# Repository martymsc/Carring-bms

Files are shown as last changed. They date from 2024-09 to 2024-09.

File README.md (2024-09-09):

# Carring-bms
Bms system for lithium based cells. Carring because it cares :D

The bms is based on an arduino leonardo board from Longan Labs (https://www.longan-labs.cc/1030008.html) and a battery monitor IC from Texas Instruments called BQ76PL455A.

Current revision:
 <ul>
  <li>  Battery cells voltage readout over serial</li>
  <li>  OV and UV protection with contactor control</li>
  <li>  Precharge circuit contorl</li>
  <li>  Isolation between contol MCU and battery  </li>
  <li>  Mcu supply is from the car, bms ic is powered by the battery </li>
 </ul> 
  
Problems:
<ul>
 <li>  Cell balancing is present but wasnt working in last revision</li>
 <li>  Same for the drain current measurment</li>
</ul>

Future goals:
<ul>
 <li>  Battery drain current measurment </li>
 <li>  Can bus logging implmentation</li>
 <li>  Switch to integrated MCU, either an STM or an RP </li>
 <li>  Fuel gauging</li>
 <li>  Charging control</li>
 <li>  Update the bms ic to a newer BQ79654</li>
 <li>  Add stackable funcionality</li>
</ul>

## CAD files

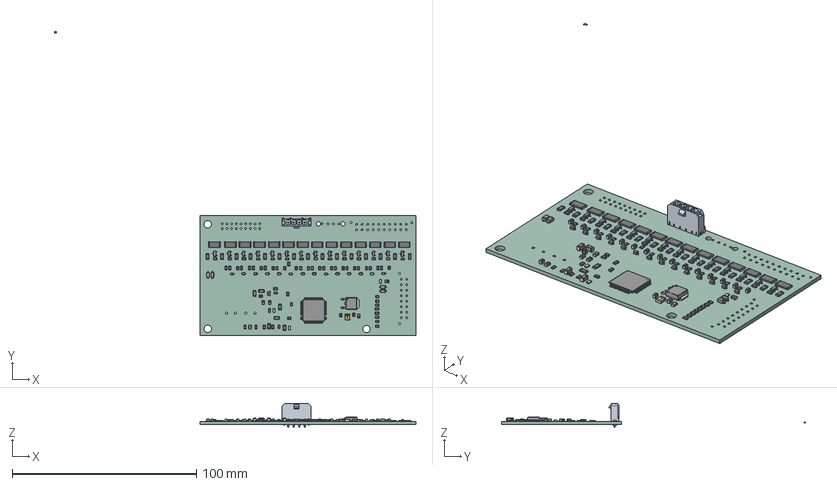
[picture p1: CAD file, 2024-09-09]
BMS v21.step
196.4 x 164.9 x 13.1 mm
ASSEMBLY x 102
CCS_CCSTD_0805_L2.2W1.45T0.88B0.5 x 6
RR1220P-103-D x 28
CCS_CCSTDNOS_1210_L3.4W2.7T1.05B0.75
ZXTN4004KQTC
RC0805FR-0727R4L x 2
PFC0080A_ASM
_autosave-BMS v21_PCB
AUTOMAPKI 1
AUTOMAPKI 2

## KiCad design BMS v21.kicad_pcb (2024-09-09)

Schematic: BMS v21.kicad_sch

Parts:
C1, C18, C22, C23, C28: C0805C104K5RACTU; C0805; Mouser Part Number 80-C0805C104K5R
C2, C3, C4, C5, C6, C7, C8, C9, C10, C11, C12, C13, C14, C15, C16, C17, C25, C30: C2012X7S2A105K125AB; CAPC2012X145N; Mouser Part Number 810-C2012X7S2A105K
C19, C21, C24, C29: GRM31CR71H475KA12L; CAPC3216X180N; Mouser Part Number 81-GRM31CR71H475KA2L
C20: VJ0805D391KXCAJ; CAPC2012X145N; Mouser Part Number 77-VJ0805D391KXCAJ
C26: C0805C223K5RACTU; C0805; Mouser Part Number 80-C0805C223K5R
C27: C1210C185K3PACTU; C1210; Manufacturer_Part_Number C1210C185K3PACTU
D1, D2, D3, D4: 1N4148W; SODFL3816X120N; Mouser Part Number 637-1N4148W
IC1: BQ76PL455APFCR; QFP50P1400X1400X120-80N; Mouser Part Number 595-BQ76PL455APFCR
J1: 66201621122; Mouser Part Number 710-66201621122
J2: 66202021122; Mouser Part Number 710-66202021122
J3, J4: 43650-0420; 43650-04YY_18192063; Mouser Part Number 538-43650-0420
LED1, LED2, LED3, LED4, LED5, LED6, LED7, LED8, LED9, LED10, LED11, LED12, LED13, LED14: APHCM2012SYCK-F01; LEDC2012X50N; Mouser Part Number 604-APHCM2012SYCK
Q1, Q2, Q3, Q4, Q5, Q6, Q7, Q8, Q9, Q10, Q11, Q12, Q13, Q14: 2V7002KT1G; SOT96P237X111-3N; Mouser Part Number 863-2V7002KT1G
Q15: ZXTN4004KQTC; Mouser Part Number 621-ZXTN4004KQTC
R1, R2, R3, R4, R5, R6, R7, R8, R82, R86, R87, R88, R89, R90: RR1220P-104-D; RESC2013X65N; Mouser Part Number 754-RR1220P-104D
R9, R10, R11, R12, R13, R14, R15, R16, R17, R18, R19, R20, R21, R22: CRGCQ2512F33R; RESC6432X65N; Mouser Part Number 279-CRGCQ2512F33R
R23, R38, R40, R42, R43, R45, R47, R49, R51, R53, R55, R57, R59, R61, R63, R91: CRCW0805200RFKEA; RESC2012X50N; Mouser Part Number 71-CRCW0805-200-E3
R24, R25, R26, R27, R28, R29, R30, R31, R32, R33, R34, R35, R36, R37: RC0805FR-07100KL; RESC2012X60N; Mouser Part Number 603-RC0805FR-07100KL
R39, R41, R44, R46, R48, R50, R52, R54, R56, R58, R60, R62, R64, R80: ERJ-6GEYJ202V; RESC2013X65N; Mouser Part Number 667-ERJ-6GEYJ202V
R65, R66, R67, R68, R69, R70, R71, R72, R73, R74, R75, R76, R77, R78, R79: ERJ-8ENF1001V; ERJ8ENF1000V; Mouser Part Number 667-ERJ-8ENF1001V
R81: CRCW080551K0FKEA; RESC2012X50N; Mouser Part Number 71-CRCW080551K0FKEA
R83, R84, R85: ERJ-6ENF51R0V; ERJ6ENF1000V; Mouser Part Number 667-ERJ-6ENF51R0V
R92, R93: CRCW0805360RFKEA; RESC2012X50N; Mouser Part Number 71-CRCW0805360RFKEA
R94: ERJ-U6QJR39V; RESC2012X60N; Mouser Part Number 603-RC0805FR-07100KL
R95, R96: ERJ-8RQF1R0V; ERJ8_B_BW_R_LW_CW_D; Mouser Part Number 667-ERJ-8RQF1R0V
U1: CANBed v1.2e
Z1, Z2, Z3, Z4, Z5, Z6, Z7, Z8, Z9, Z10, Z11, Z12, Z13, Z14: MM3Z6V2T1G; SOD2512X110N; Mouser Part Number 863-MM3Z6V2T1G

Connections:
/+5V: U1.18 (5V)
/Arduino power on: J3.1, J4.4, U1.19 (VIN)
/Ballance1: IC1.28 (EQ1), R64.2 (R2)
/Ballance2: IC1.26 (EQ2), R62.2 (R2)
/Ballance3: IC1.24 (EQ3), R60.2 (R2)
/Ballance4: IC1.22 (EQ4), R58.2 (R2)
/Ballance5: IC1.20 (EQ5), R56.2 (R2)
/Ballance6: IC1.18 (EQ6), R54.2 (R2)
/Ballance7: IC1.16 (EQ7), R52.2 (R2)
/Ballance8: IC1.14 (EQ8), R50.2 (R2)
/Ballance9: IC1.12 (EQ9), R48.2 (R2)
/Ballance10: IC1.10 (EQ10), R46.2 (R2)
/Ballance11: IC1.8 (EQ11), R44.2 (R2)
/Ballance12: IC1.6 (EQ12), R80.1 (R1)
/Ballance13: IC1.4 (EQ13), R41.2 (R2)
/Ballance14: IC1.2 (EQ14), R39.2 (R2)
/CAN H: J3.4, U1.21 (CANH)
/CAN L: J3.3, U1.22 (CANL)
/Current_sense_OUT: U1.12 (A0)
/FALUT_N: R83.2, U1.2 (D4)
/NPN_BASE: IC1.71 (NPNB), Q15.1 (B)
/OUT: C20.1, IC1.68 (OUT2), IC1.73 (OUT1)
/Precharge IN: J4.2, U1.15 (D11)
/Precharge OUT: J4.1, U1.13 (D10)
/RX: R84.2, R88.1 (R1), U1.3 (D1/TX)
/TX: R85.2, R89.1 (R1), U1.1 (D0/RX)
/TempIN1: IC1.66 (AUX0), J1.9, R1.1 (R1)
/TempIN2: IC1.65 (AUX1), J1.10, R2.1 (R1)
/TempIN3: IC1.64 (AUX2), J1.11, R3.1 (R1)
/TempIN4: IC1.63 (AUX3), J1.12, R4.1 (R1)
/TempIN5: IC1.62 (AUX4), J1.13, R5.1 (R1)
/TempIN6: IC1.61 (AUX5), J1.14, R6.1 (R1)
/TempIN7: IC1.60 (AUX6), J1.15, R7.1 (R1)
/TempIN8: IC1.59 (AUX7), J1.16, R8.1 (R1)
/V5VAO: C24.1, IC1.58 (V5VAO), R87.1 (R1)
/VDIG: C18.2, C21.2, IC1.34 (VDIG), R95.1
/VIO: C23.2, C25.2, IC1.41 (VIO), R88.2 (R2), R89.2 (R2), R96.1
/VP1: IC1.70 (VP), Q15.3 (E), R1.2 (R2), R2.2 (R2), R3.2 (R2), R4.2 (R2), R5.2 (R2), R6.2 (R2), R7.2 (R2), R8.2 (R2), R94.2, R95.2, R96.2
/Vsense1(4.2V): J2.18, Q13.3 (D), R22.2, R36.1, R78.1
/Vsense1_OUT: C15.2, IC1.27 (VSENSE1), LED14.2 (A), R78.2, Z13.2 (A), Z14.1 (K); also elsewhere on the board
/Vsense2(8.4V): J2.8, Q12.3 (D), R21.2, R35.1, R77.1
/Vsense2_OUT: C14.2, IC1.25 (VSENSE2), LED13.2 (A), R77.2, Z12.2 (A), Z13.1 (K); also elsewhere on the board
/Vsense3(12.6V): J2.17, Q11.3 (D), R20.2, R34.1, R76.1
/Vsense3_OUT: C13.2, IC1.23 (VSENSE3), LED12.2 (A), R76.2, Z11.2 (A), Z12.1 (K); also elsewhere on the board
/Vsense4(16.8V): J2.7, Q10.3 (D), R19.2, R33.1, R75.1
/Vsense4_OUT: C12.2, IC1.21 (VSENSE4), LED11.2 (A), R75.2, Z10.2 (A), Z11.1 (K); also elsewhere on the board
/Vsense5(21V): J2.16, Q9.3 (D), R18.2, R32.1, R74.1
/Vsense5_OUT: C11.2, IC1.19 (VSENSE5), LED10.2 (A), R74.2, Z9.2 (A), Z10.1 (K); also elsewhere on the board
/Vsense6(25.2V): J2.6, Q8.3 (D), R17.2, R31.1, R73.1
/Vsense6_OUT: C10.2, IC1.17 (VSENSE6), LED9.2 (A), R73.2, Z8.2 (A), Z9.1 (K); also elsewhere on the board
/Vsense7(29.4V): J2.15, Q7.3 (D), R16.2, R30.1, R72.1
/Vsense7_OUT: C9.2, IC1.15 (VSENSE7), LED8.2 (A), R72.2, Z7.2 (A), Z8.1 (K); also elsewhere on the board
/Vsense8(33.6V): J2.5, Q6.3 (D), R15.2, R29.1, R71.1
/Vsense8_OUT: C8.2, IC1.13 (VSENSE8), LED7.2 (A), R71.2, Z6.2 (A), Z7.1 (K); also elsewhere on the board
/Vsense9(37.8V): J2.14, Q5.3 (D), R14.2, R28.1, R70.1
/Vsense9_OUT: C7.2, IC1.11 (VSENSE9), LED6.2 (A), R70.2, Z5.2 (A), Z6.1 (K); also elsewhere on the board
/Vsense10(42V): J2.4, Q4.3 (D), R13.2, R27.1, R69.1
/Vsense10_OUT: C6.2, IC1.9 (VSENSE10), LED5.2 (A), R69.2, Z4.2 (A), Z5.1 (K); also elsewhere on the board
/Vsense11(46.2V): J2.13, Q3.3 (D), R12.2, R26.1, R68.1
/Vsense11_OUT: C5.2, IC1.7 (VSENSE11), LED4.2 (A), R68.2, Z3.2 (A), Z4.1 (K); also elsewhere on the board
/Vsense12(50.4V): J2.3, Q2.3 (D), R11.2, R25.1, R67.1
/Vsense12_OUT: C4.2, IC1.5 (VSENSE12), LED3.2 (A), R67.2, Z2.2 (A), Z3.1 (K); also elsewhere on the board
/Vsense13(54.6V): J2.12, Q1.3 (D), R10.2, R24.1, R66.1
/Vsense13_OUT: C3.2, IC1.3 (VSENSE13), LED2.2 (A), R66.2, Z1.2 (A), Z2.1 (K); also elsewhere on the board
/Vsense14(58.8V): J2.1, J2.2, J2.11, R9.2, R23.1, R65.1, R92.2
/WAKEUP: R91.2, U1.4 (D5)
unnamed: C29.2, R94.1
unnamed: C26.2, IC1.33 (CHM)
unnamed: C26.1, IC1.32 (CHP)
unnamed: IC1.52 (COMML+), R87.2 (R2)
unnamed: IC1.53 (COMML-), R86.2 (R2)
unnamed: IC1.40 (FAULT__N), R81.1, R83.1
unnamed: IC1.42 (GPIO5), IC1.43 (GPIO4), IC1.44 (GPIO3), IC1.45 (GPIO2), IC1.46 (GPIO1), IC1.47 (GPIO0), R82.1 (R1)
unnamed: IC1.39 (RX), R84.1
unnamed: IC1.38 (TX), R85.1
unnamed: C19.2, C22.2, IC1.31 (VM)
unnamed: C27.2, C28.2, IC1.67 (VR_EF)
unnamed: IC1.49 (WAKEUP), R90.2 (R2), R91.1
unnamed 78: LED1.1 (K), R38.2; also elsewhere on the board
unnamed 79: LED2.1 (K), R40.2; also elsewhere on the board
unnamed 80: LED3.1 (K), R42.2; also elsewhere on the board
unnamed 81: LED4.1 (K), R43.2; also elsewhere on the board
unnamed 82: LED5.1 (K), R45.2; also elsewhere on the board
unnamed 83: LED6.1 (K), R47.2; also elsewhere on the board
unnamed 84: LED7.1 (K), R49.2; also elsewhere on the board
unnamed 85: LED8.1 (K), R51.2; also elsewhere on the board
unnamed 86: LED9.1 (K), R53.2; also elsewhere on the board
unnamed 87: LED10.1 (K), R55.2; also elsewhere on the board
unnamed 88: LED11.1 (K), R57.2; also elsewhere on the board
unnamed 89: LED12.1 (K), R59.2; also elsewhere on the board
unnamed 90: LED13.1 (K), R61.2; also elsewhere on the board
unnamed 91: LED14.1 (K), R63.2; also elsewhere on the board
unnamed: Q1.1 (G), R24.2, R39.1 (R1)
unnamed: Q1.2 (S), R9.1, R38.1
unnamed: Q2.1 (G), R25.2, R41.1 (R1)
unnamed: Q2.2 (S), R10.1, R40.1
unnamed: Q3.1 (G), R26.2, R80.2 (R2)
unnamed: Q3.2 (S), R11.1, R42.1
unnamed: Q4.1 (G), R27.2, R44.1 (R1)
unnamed: Q4.2 (S), R12.1, R43.1
unnamed: Q5.1 (G), R28.2, R46.1 (R1)
unnamed: Q5.2 (S), R13.1, R45.1
unnamed: Q6.1 (G), R29.2, R48.1 (R1)
unnamed: Q6.2 (S), R14.1, R47.1
unnamed: Q7.1 (G), R30.2, R50.1 (R1)
unnamed: Q7.2 (S), R15.1, R49.1
unnamed: Q8.1 (G), R31.2, R52.1 (R1)
unnamed: Q8.2 (S), R16.1, R51.1
unnamed: Q9.1 (G), R32.2, R54.1 (R1)
unnamed: Q9.2 (S), R17.1, R53.1
unnamed: Q10.1 (G), R33.2, R56.1 (R1)
unnamed: Q10.2 (S), R18.1, R55.1
unnamed: Q11.1 (G), R34.2, R58.1 (R1)
unnamed: Q11.2 (S), R19.1, R57.1
unnamed: Q12.1 (G), R35.2, R60.1 (R1)
unnamed: Q12.2 (S), R20.1, R59.1
unnamed: Q13.1 (G), R36.2, R62.1 (R1)
unnamed: Q13.2 (S), R21.1, R61.1
unnamed: Q14.1 (G), R37.2, R64.1 (R1)
unnamed: Q14.2 (S), R22.1, R63.1
unnamed: C30.1, Q15.2 (C), R93.1
unnamed: R92.1, R93.2

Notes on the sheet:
Konektor pro tep. sondy
Konnektor pro balancování a nabíjení

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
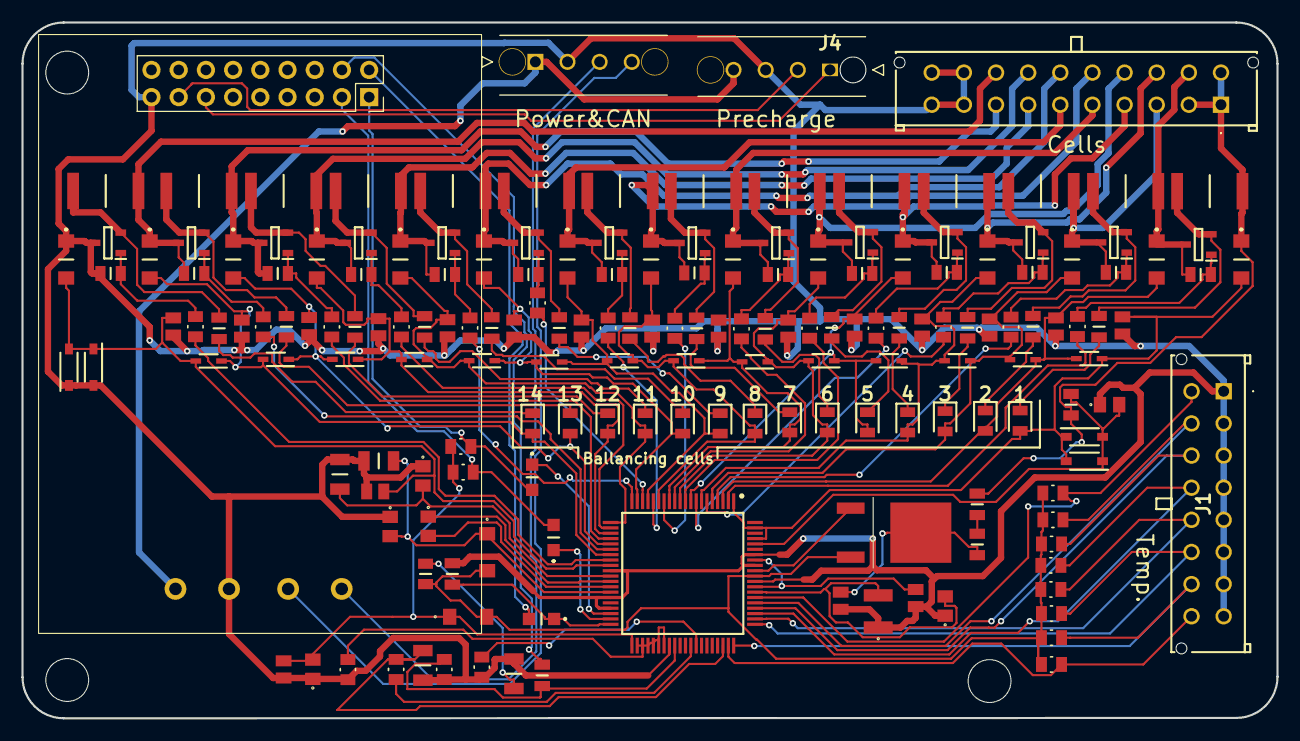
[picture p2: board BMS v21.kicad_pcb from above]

Board: 2 copper layers, 117.2 x 65.0 mm, 179 parts (0 on the bottom side), 124 nets.

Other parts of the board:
1, 2, 3, 4, 5, 6, 7, 8, 9, 10, 11, 12, 13, 14: APHCM2012SYCK-F01; LEDC2012X50N

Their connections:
/Vsense1_OUT: 14.2 (A); also elsewhere on the board
/Vsense2_OUT: 13.2 (A); also elsewhere on the board
/Vsense3_OUT: 12.2 (A); also elsewhere on the board
/Vsense4_OUT: 11.2 (A); also elsewhere on the board
/Vsense5_OUT: 10.2 (A); also elsewhere on the board
/Vsense6_OUT: 9.2 (A); also elsewhere on the board
/Vsense7_OUT: 8.2 (A); also elsewhere on the board
/Vsense8_OUT: 7.2 (A); also elsewhere on the board
/Vsense9_OUT: 6.2 (A); also elsewhere on the board
/Vsense10_OUT: 5.2 (A); also elsewhere on the board
/Vsense11_OUT: 4.2 (A); also elsewhere on the board
/Vsense12_OUT: 3.2 (A); also elsewhere on the board
/Vsense13_OUT: 2.2 (A); also elsewhere on the board
unnamed 78: 1.1 (K); also elsewhere on the board
unnamed 79: 2.1 (K); also elsewhere on the board
unnamed 80: 3.1 (K); also elsewhere on the board
unnamed 81: 4.1 (K); also elsewhere on the board
unnamed 82: 5.1 (K); also elsewhere on the board
unnamed 83: 6.1 (K); also elsewhere on the board
unnamed 84: 7.1 (K); also elsewhere on the board
unnamed 85: 8.1 (K); also elsewhere on the board
unnamed 86: 9.1 (K); also elsewhere on the board
unnamed 87: 10.1 (K); also elsewhere on the board
unnamed 88: 11.1 (K); also elsewhere on the board
unnamed 89: 12.1 (K); also elsewhere on the board
unnamed 90: 13.1 (K); also elsewhere on the board
unnamed 91: 14.1 (K); also elsewhere on the board

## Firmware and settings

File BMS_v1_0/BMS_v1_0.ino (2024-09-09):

//zpráva synchronizující komunikaci
byte messageSync[] = {0xF1, 0x02, 0x00, 0x50, 0x93};
//zpráva vracející počet vzorkovaných článků
byte messagerespodNumOfcells[] = {0x81, 0x00, 0x0D, 0x01, 0xED, 0x6C}; //works
//91 00 14 00 23FC
byte messageDisablBall[] = {0x91, 0x00, 0x20, 0x00, 0x35, 0x3C};

//Zpráva která přečte registry, vrací hodnoty nastavené podle adesy kanálu
byte messageReadVoltage1[] = {0xE1, 0x02, 0x00, 0x51, 0x56};

//Nastavení vzorkovací frekvence ADC
byte messageSetSampleRate[] = {0x91, 0x00, 0x62, 0xFF, 0x45, 0xDC};

// Adresy kanálů napětí
 byte messageSetSampledChannels1[] = {0x94, 0x00, 0x03, 0x10, 0x00, 0x00, 0x00, 0x95, 0x09 }; // adresa13
 byte messageSetSampledChannels2[] = {0x94, 0x00, 0x03, 0x20, 0x00, 0x00, 0x00, 0x9A, 0x09 };  // adresa14
 byte messageSetSampledChannels3[] = {0x94, 0x00, 0x03, 0x08, 0x00, 0x00, 0x00, 0x93, 0xA9}; // adresa1
 byte messageSetSampledChannels4[] = {0x94, 0x00, 0x03, 0x04, 0x00, 0x00, 0x00, 0x90, 0xF9}; // adresa2
 byte messageSetSampledChannels5[] = {0x94, 0x00, 0x03, 0x02, 0x00, 0x00, 0x00, 0x90, 0x71}; // adresa3
 byte messageSetSampledChannels6[] = {0x94, 0x00, 0x03, 0x01, 0x00, 0x00, 0x00, 0x90, 0x35}; // adresa4
 byte messageSetSampledChannels7[] = {0x94, 0x00, 0x03, 0x00, 0x80, 0x00, 0x00, 0x90, 0x21}; // adresa5
 byte messageSetSampledChannels8[] = {0x94, 0x00, 0x03, 0x00, 0x40, 0x00, 0x00, 0x90, 0xD1}; // adresa6
 byte messageSetSampledChannels9[] = {0x94, 0x00, 0x03, 0x00, 0x20, 0x00, 0x00, 0x90, 0x03}; // adresa7
 byte messageSetSampledChannels10[] = {0x94, 0x00, 0x03, 0x00, 0x10, 0x00, 0x00, 0x90, 0x0C}; // adresa8
 byte messageSetSampledChannels11[] = {0x94, 0x00, 0x03, 0x00, 0x08, 0x00, 0x00, 0x10, 0x0B}; // adresa9
 byte messageSetSampledChannels12[] = {0x94, 0x00, 0x03, 0x00, 0x04, 0x00, 0x00, 0xD0, 0x08}; // adresa10
 byte messageSetSampledChannels13[] = {0x94, 0x00, 0x03, 0x00, 0x02, 0x00, 0x00, 0x30, 0x09}; // adresa11
 byte messageSetSampledChannels14[] = {0x94, 0x00, 0x03, 0x00, 0x01, 0x00, 0x00, 0xC0, 0x09}; // adresa12
// Adresy kanálů teplotních čidel

 byte messageSetSampledChannels17[] = {0x94, 0x00, 0x03, 0x00, 0x00, 0x80, 0x00, 0xF0, 0x09}; //x 
 byte messageSetSampledChannels18[] = {0x94, 0x00, 0x03, 0x00, 0x00, 0x40, 0x00, 0xA0, 0x09}; //tep1
 byte messageSetSampledChannels19[] = {0x94, 0x00, 0x03, 0x00, 0x00, 0x20, 0x00, 0x88, 0x09}; //tep 2
 byte messageSetSampledChannels20[] = {0x94, 0x00, 0x03, 0x00, 0x00, 0x10, 0x00, 0x9C, 0x09}; //tep 3
 byte messageSetSampledChannels21[] = {0x94, 0x00, 0x03, 0x00, 0x00, 0x08, 0x00, 0x96, 0x09}; // tep 4
 byte messageSetSampledChannels22[] = {0x94, 0x00, 0x03, 0x00, 0x00, 0x04, 0x00, 0x93, 0x09}; //tep 5
 byte messageSetSampledChannels23[] = {0x94, 0x00, 0x03, 0x00, 0x00, 0x02, 0x00, 0x90, 0xA9}; //tep 6
 byte messageSetSampledChannels24[] = {0x94, 0x00, 0x03, 0x00, 0x00, 0x01, 0x00, 0x90, 0x59}; // tep 7
 byte messageSetSampledChannels25[] = {0x94, 0x00, 0x03, 0x00, 0x00, 0x00, 0x80, 0x90, 0x69}; // adresa25 x
 byte messageSetSampledChannels26[] = {0x94, 0x00, 0x03, 0x00, 0x00, 0x00, 0x40, 0x90, 0x39}; // adresa26 x
 byte messageSetSampledChannels27[] = {0x94, 0x00, 0x03, 0x00, 0x00, 0x00, 0x20, 0x90, 0x11}; // adresa27 x
 byte messageSetSampledChannels28[] = {0x94, 0x00, 0x03, 0x00, 0x00, 0x00, 0x10, 0x90, 0x05}; // adresa28 tep1
 byte messageSetSampledChannels29[] = {0x94, 0x00, 0x03, 0x00, 0x00, 0x00, 0x08, 0x90, 0x0F}; // adresa29 x
 byte messageSetSampledChannels30[] = {0x94, 0x00, 0x03, 0x00, 0x00, 0x00, 0x04, 0x90, 0x0A}; // adresa30 x
 byte messageSetSampledChannels31[] = {0x94, 0x00, 0x03, 0x00, 0x00, 0x00, 0x02, 0x10, 0x08}; // adresa31 x
 byte messageSetSampledChannels32[] = {0x94, 0x00, 0x03, 0x00, 0x00, 0x00, 0x01, 0x50, 0x09}; // adresa32 x



bool TempFlag = 0;
bool UnderVoltageFlag = 0;
bool contactor = 0;


String data = " "; // string obsahující přečtená data kanálu
String AllData = " "; // soubor všech hodnot na čtených kanálech, pro výpis
String StringToPrint = " ";
int currentChannel = 0; // Index aktuálního kanálu


double resistance = 0;
double temperature = 0;



void setup() {
  Serial.begin(250000);
  Serial1.begin(250000);
  pinMode(5, OUTPUT);
  pinMode(13, OUTPUT);
  pinMode(11, OUTPUT);
  delay(1000);
  Serial.println("wake up");
  digitalWrite(5, HIGH);
  delay(2000);
  Serial.println("sending message");
  delay(1000);
  Serial1.write(messageSetSampleRate, sizeof(messageSetSampleRate));
  delay(1000);
  //inicializace displaye
  delay(100);
   
    
}

void loop() {

if(TempFlag == 1){
  //vypnutí stykače
    digitalWrite(11, LOW);
    contactor = 0;
}

if(UnderVoltageFlag == 1){
  //vypnutí stykače
    digitalWrite(11, LOW);
}

  
  ChannelWrite(currentChannel);
  delay(100);
  Serial1.write(messageReadVoltage1, sizeof(messageReadVoltage1));
  delay(100);
  while (Serial1.available()) {
    while (Serial1.available()) {
    
    data += String(Serial1.read(),HEX);
    
   }
 
   data.remove(6);
   data.remove(1,1);
   unsigned int decValue = strtol(data.c_str(), NULL, 16);
   double voltage = 2.0 * 2.5 / 65535.0 * decValue;
  if (currentChannel > 14) {
      resistance = calculateResistance(voltage);
      temperature = calculateTemperature(resistance);
 
 //Vztyčení flagu o přehřáítí
      if(temperature > 63){
        TempFlag = 1;
        }
    }
 /*
   StringToPrint += "Cell";
   StringToPrint += (currentChannel + 1);
   StringToPrint += ":";
   if(currentChannel < 15){
   StringToPrint += String(voltage,3);
   */
   
  if(currentChannel < 14){
   StringToPrint += "Cell";
   StringToPrint += (currentChannel + 1);
   StringToPrint += ":";

//vztyčení flagu o podvybití
  if(voltage < 3){
    UnderVoltageFlag = 1;
    }
   
   StringToPrint += String(voltage,3);
  }
   if(currentChannel > 13){
   StringToPrint += "Temp";
   StringToPrint += (currentChannel +1);
   StringToPrint += ":";
   StringToPrint += String(temperature,3);
   }
  
//výpis aktuálního kanálu na terminal, jeho reset a přidání do celkového řetězce
    Serial.println(StringToPrint);
     AllData += StringToPrint;
    StringToPrint = " ";

  //reset proměnné data a inkrementace pro měření dalšího kanálu
   data = " ";
   currentChannel++;

   //reset měřeného kanálu
   if(currentChannel>20){
     currentChannel = 0;
   //výpis dat na display
    Serial.println(AllData);
    
    //reset stringu obsahující napětí článků a teploty
    AllData = "";
   }
   }
   
   if(TempFlag == 0 & UnderVoltageFlag == 0){
        digitalWrite(11, HIGH);
   }
}
   
void ChannelWrite(int ChannelAdress){
  switch(ChannelAdress){
    case 0:
      Serial1.write(messageSetSampledChannels1, sizeof(messageSetSampledChannels1));
      break;
    case 1:
      Serial1.write(messageSetSampledChannels2, sizeof(messageSetSampledChannels2));
      break;
    case 2:
      Serial1.write(messageSetSampledChannels3, sizeof(messageSetSampledChannels3));
      break;
    case 3:
      Serial1.write(messageSetSampledChannels4, sizeof(messageSetSampledChannels4));
      break;
    case 4:
      Serial1.write(messageSetSampledChannels5, sizeof(messageSetSampledChannels5));
      break;
    case 5:
      Serial1.write(messageSetSampledChannels6, sizeof(messageSetSampledChannels6));
      break;
    case 6:
      Serial1.write(messageSetSampledChannels7, sizeof(messageSetSampledChannels7));
      break;
    case 7:
      Serial1.write(messageSetSampledChannels8, sizeof(messageSetSampledChannels8));
      break;
    case 8:
      Serial1.write(messageSetSampledChannels9, sizeof(messageSetSampledChannels9));
      break;
    case 9:
      Serial1.write(messageSetSampledChannels10, sizeof(messageSetSampledChannels10));
      break;
    case 10:
      Serial1.write(messageSetSampledChannels11, sizeof(messageSetSampledChannels11));
      break;
    case 11:
      Serial1.write(messageSetSampledChannels12, sizeof(messageSetSampledChannels12));
      break;
    case 12:
      Serial1.write(messageSetSampledChannels13, sizeof(messageSetSampledChannels13));
      break;
    case 13:
      Serial1.write(messageSetSampledChannels14, sizeof(messageSetSampledChannels14));
      break;   
    case 14:
      Serial1.write(messageSetSampledChannels18, sizeof(messageSetSampledChannels18));
      break;  
    case 15:
      Serial1.write(messageSetSampledChannels19, sizeof(messageSetSampledChannels19));
      break;   
    case 16:
      Serial1.write(messageSetSampledChannels20, sizeof(messageSetSampledChannels20));
      break;
    case 17:
      Serial1.write(messageSetSampledChannels21, sizeof(messageSetSampledChannels21));
      break;
    case 18:
     Serial1.write(messageSetSampledChannels22, sizeof(messageSetSampledChannels22));
      break;   
    case 19:
      Serial1.write(messageSetSampledChannels23, sizeof(messageSetSampledChannels23));
      break;  
    case 20:
      Serial1.write(messageSetSampledChannels24, sizeof(messageSetSampledChannels24));
      break;   
    
  }
}

double calculateTemperature(double resistance) {
  double R25 = 100000.0;    // Hodnota odporu při 25°C
  double B25_50 = 3950.0;   // Hodnota B při 25/50°C

  double invTemperature = 1.0 / (1.0 / 298.15 + (1.0 / B25_50) * log(resistance / R25));
  double temperature = invTemperature - 273.15; // Převod na °C
  return temperature;
}
double calculateResistance(double voltage) {
  // Přepočet na odporový dělič se známou hodnotou rezistoru
  double resistorValue = 100000.0; // Hodnota rezistoru v ohmech
  double resistance = resistorValue * voltage / (5 - voltage);
  return resistance;
}

 
